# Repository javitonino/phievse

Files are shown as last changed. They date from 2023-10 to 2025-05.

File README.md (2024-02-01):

# ϕ-EVSE

An electric vehicle "charger" (EVSE) that can automatically switch between 1 and 3 phase charging.

**This is a personal learning project and it's not production ready. Use it at your own risk.** That said, this might be interesting to learn how this devices work.
Since I was learning myself when I designed this, it should be relatively easy to understand.

## Features

The main differentiator (and motivation for the project) is the ability to switch between 1-phase and 3-phase charging, thus supporting the full range of charging powers.
In the case of 230V AC, this means from 1.4kW (1 phase, 6A) to 22kW (3 phase, 32A).

Charging power can be controlled via web interface or MQTT (integrated with HomeAssistant).

## Anti-features (you really shouldn't connect your car to this)

Although there are safety checks in place (pilot and relay checks), I haven't been able to test them outside of lab conditions. As such, this should not be considered a safe product to use,
which is not ideal (to say the least) for something called Electric Vehicle Safety Equipment.

In general, I lost interest in the project once it behaved well enough to fulfill my needs, so things are not as stable as they should. 

Finally, there are some decisions (documented in the READMEs for [hardware](hardware/README.md) and [firmware](firmware/README.md)) that are not really good ideas and were done in an effort to understand why nobody
else was doing it that way.

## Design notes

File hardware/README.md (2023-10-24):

# ϕ-EVSE hardware

These are the schematics for the ϕ-EVSE project. See also the [project README](../README.md).

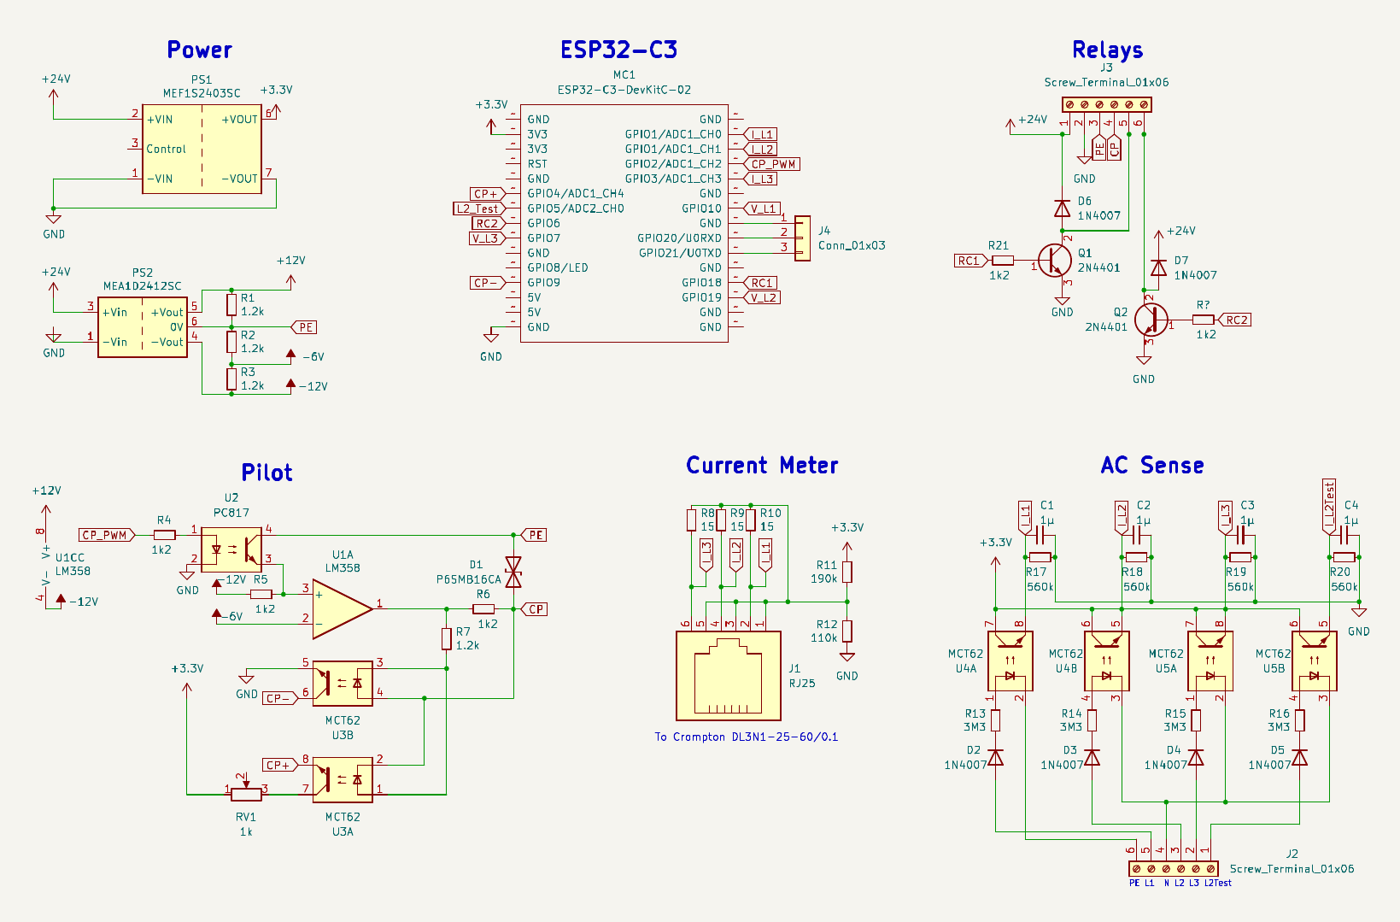
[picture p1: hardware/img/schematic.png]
Schematics


## Design notes

- The device is controlled by an ESP32-C3 microcontroller. In this case, it's using a devkit mounted into a prototype board.
- The power system generates 24V (for the relays), ±12V (for the control pilot) and 3.3V (for the electronics).
- The control pilot circuitry is optically isolated from the car. This difers from the standard control circuit and adding optocouples caused issues with switching speed and accurately setting the duty cycle.
- There is a current meter using a current transformer and shunt resistor connected to an ADC pin for each phase.
- There are four AC sensors (optocouplers with a capacitor for smoothing the signal). Three of them check the output of the relay (to check for stuck relays) and the forth one is used to check if 3-phase power is available at the input.

## Mounting

Everything is mounted on a DIN rail inside a CamdemBoss CHDX6-230 enclosure:
- 24V power supply, no special requirements.
- Enclosure for the electronic (CamdemBoss CNMB/2/KIT)
- Main power contactor: 4-pole contactor. Using Finder 22.74.0.024.1310 for the small size while supporting 32A.
- 1-3 phase contactor: 2-pole contactor. Using Finder 22.72.0.024.1310 for the small size while supporting 32A.

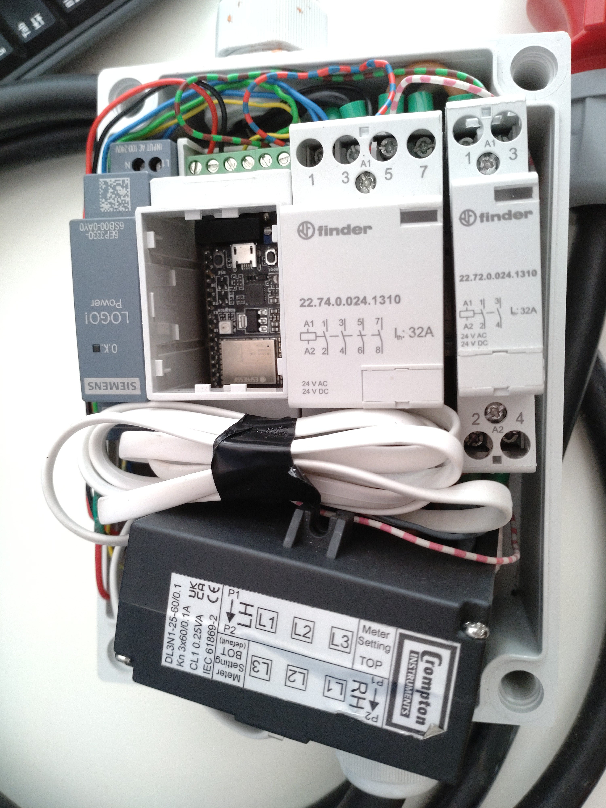
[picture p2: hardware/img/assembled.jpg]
Assembled EVSE


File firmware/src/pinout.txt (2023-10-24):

+24V    0V     PE     Pilot      R(18)     R(6)

RJ25   PE  Lpe(10)  N  Ln(19)  Ln(7)  Ln(5)

GPIO
====

In (analog)
-----------
Current Meter: 0, 1, 3
Pilot+: 4

In (digital)
------------
Voltage Meter (PE): 10
Voltage Meter (N): 19, 7, 5
Pilot-: 9

Out
---
LED: 8
Relays: 18, 6
PWM Pilot: 2

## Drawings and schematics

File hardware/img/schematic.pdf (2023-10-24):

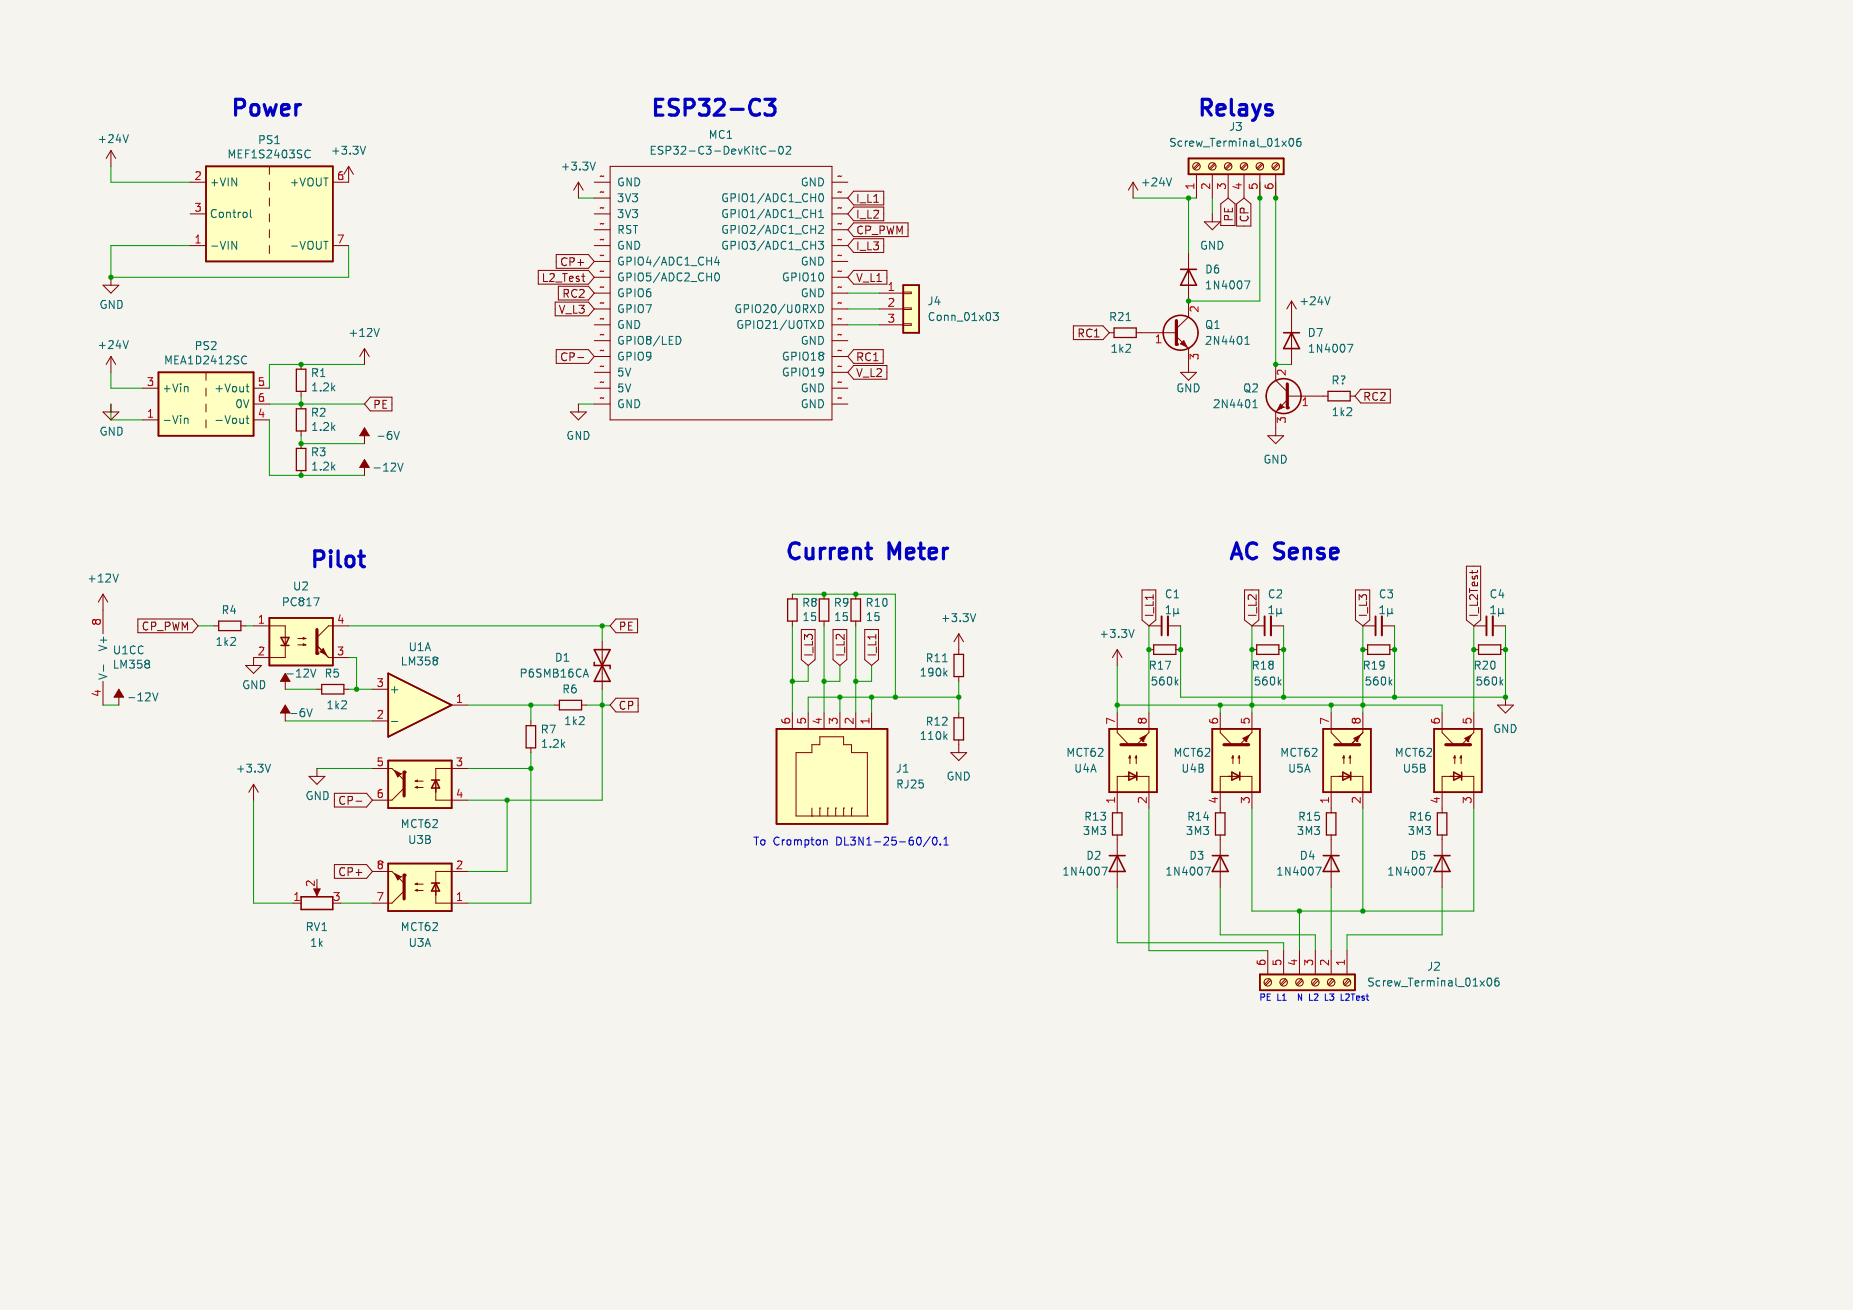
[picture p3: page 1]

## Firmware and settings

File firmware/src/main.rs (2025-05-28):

#![allow(unexpected_cfgs)]

use embedded_svc::ipv4::Configuration;
use embedded_svc::wifi::AccessPointConfiguration;
use esp_idf_hal::gpio::{PinDriver, Pull};
use esp_idf_hal::ledc::config::TimerConfig;
use esp_idf_hal::ledc::{LedcDriver, LedcTimerDriver, Resolution};
use esp_idf_hal::prelude::*;
use esp_idf_svc::eventloop::EspSystemEventLoop;
use esp_idf_svc::netif::{EspNetif, NetifConfiguration};
use esp_idf_svc::sntp::EspSntp;
use esp_idf_svc::wifi::WifiDriver;
use esp_idf_sys::*;
use phievse::driver::gpio::InterruptPin;
use phievse::gpio::RelayPin;
use phievse::*;
use std::error::Error;

// Using as library
use phievse::driver::{adc::*, watchdog::*};
use phievse::logger::RingBufferLogger;

// Using directly
mod config;
mod httpd;
mod mqtt;

use embedded_svc::{ipv4::DHCPClientSettings, wifi::ClientConfiguration};
use esp_idf_svc::{netif::NetifStack, wifi::EspWifi};

use crate::config::*;

esp_idf_sys::esp_app_desc! {}

fn main() -> Result<(), Box<dyn Error>> {
    // Disables USB JTAG on GPIO 18/19. Allows to disable pullups in those pins.
    unsafe {
        let usb_jtag_reg: *mut u32 = 1610887192 as *mut u32;
        let mask_bit_9 = u32::MAX - (1 << 9);
        *usb_jtag_reg &= mask_bit_9;
    }

    esp_idf_svc::sys::link_patches();

    // Set maximum priority after timers and driver code
    // Other spawned threads (e.g: LEDController) default to 5 unless changed
    unsafe { vTaskPrioritySet(std::ptr::null_mut(), 19) };

    // Initialize esp-idf-svc logger
    // EspLogger::initialize_default();

    // Initialize our in-memory logger
    let ring_logger: Box<RingBufferLogger> = Default::default();
    let ring_buffer = ring_logger.buffer.clone();
    log::set_boxed_logger(ring_logger)?;
    log::set_max_level(log::LevelFilter::Info);
    println!("Started logger");

    unsafe {
        let cfg = esp_pthread_cfg_t {
            stack_size: 4096,
            prio: 5,
            inherit_cfg: false,
            thread_name: std::ptr::null(),
            pin_to_core: 0,
        };
        esp_pthread_set_cfg(&cfg);
    }

    // Initialize all peripherals and the controller
    let peripherals = esp_idf_hal::peripherals::Peripherals::take().unwrap();
    let pins = peripherals.pins;

    let timer = LedcTimerDriver::new(
        peripherals.ledc.timer0,
        &TimerConfig::default()
            .frequency(1.kHz().into())
            .resolution(Resolution::Bits14),
    )?;

    let mut g10 = PinDriver::input(pins.gpio10)?;
    g10.set_pull(Pull::Floating)?;
    let mut g19 = PinDriver::input(pins.gpio19)?;
    g19.set_pull(Pull::Floating)?;
    let mut g7 = PinDriver::input(pins.gpio7)?;
    g7.set_pull(Pull::Floating)?;
    let mut g5 = PinDriver::input(pins.gpio5)?;
    g5.set_pull(Pull::Floating)?;
    let mut g9 = PinDriver::input(pins.gpio9)?;
    g9.set_pull(Pull::Up)?;

    let relay_main = RelayPin::new(LedcDriver::new(
        peripherals.ledc.channel1,
        &timer,
        pins.gpio6,
    )?);
    let relay_3_phase = RelayPin::new(LedcDriver::new(
        peripherals.ledc.channel2,
        &timer,
        pins.gpio18,
    )?);
    let analog = AdcDmaDriver::new(
        peripherals.adc1,
        pins.gpio3,
        pins.gpio1,
        pins.gpio0,
        pins.gpio4,
    )?;

    let control_pilot = LedcDriver::new(peripherals.ledc.channel0, &timer, pins.gpio2)?;
    let pilot_negative = InterruptPin::new(g9);
    let controller = Box::new(PhiEvseController::new(PhiEvsePeripherals {
        relay_main,
        relay_3_phase,
        v_sense: (g10, g19, g7),
        v_sense_3_phase: g5,
        analog,
        control_pilot,
        pilot_negative,
        watchdog: EspWatchdog,
    }));

    // Load configuration from NVS
    let config = PhiEvseConfig::load()?;
    println!("{config:#?}");

    // Build Wifi configurations
    let mut ap_config = AccessPointConfiguration {
        ssid: config.ap.ssid.as_str().try_into().unwrap(),
        ..Default::default()
    };
    if let Some(password) = config.ap.psk {
        ap_config.auth_method = embedded_svc::wifi::AuthMethod::WPA2Personal;
        ap_config.password = password.as_str().try_into().unwrap();
    }

    let mut needs_connect = false;
    let wifi_config = if let Some(sta) = config.sta {
        let mut sta_config = ClientConfiguration {
            ssid: sta.ssid.as_str().try_into().unwrap(),
            ..Default::default()
        };
        needs_connect = true;
        if let Some(password) = sta.psk {
            sta_config.auth_method = embedded_svc::wifi::AuthMethod::WPA2Personal;
            sta_config.password = password.as_str().try_into().unwrap();
        }

        embedded_svc::wifi::Configuration::Mixed(sta_config, ap_config)
    } else {
        embedded_svc::wifi::Configuration::AccessPoint(ap_config)
    };

    // Initialize Wifi
    let mut wifi_client_conf = NetifConfiguration::wifi_default_client();
    wifi_client_conf.ip_configuration = Some(Configuration::Client(
        embedded_svc::ipv4::ClientConfiguration::DHCP(DHCPClientSettings {
            hostname: Some(config.hostname.as_str().try_into().unwrap()),
        }),
    ));
    let wifi = Box::new(EspWifi::wrap_all(
        WifiDriver::new(peripherals.modem, EspSystemEventLoop::take()?, None)?,
        EspNetif::new_with_conf(&wifi_client_conf)?,
        EspNetif::new(NetifStack::Ap)?,
    )?);
    let wifi = Box::leak(wifi);
    wifi.set_configuration(&wifi_config)?;
    wifi.start()?;
    if needs_connect {
        wifi.connect()?;
    }

    // NTP
    let _ntp = EspSntp::new_default();

    // Initialize HTTP server
    println!("Starting HTTPd");
    let _h = httpd::start(
        ring_buffer,
        controller.status(),
        controller.control_channel(),
    )?;
    println!("HTTP running");

    if let Some(uri) = config.mqtt_uri {
        mqtt::start(&uri, controller.status(), controller.control_channel())?;
    }

    // Run
    Box::leak(controller).run();

    #[allow(unreachable_code)]
    Ok(())
}

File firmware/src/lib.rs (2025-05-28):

use adc::{AdcChannel, AdcSubscriber};
use control_pilot::{ControlPilotMode, ControlPilotReader, ControlPilotSignal, set_control_pilot};
use current_meter::CurrentMeter;
use embedded_hal::{PwmPin, digital::v2::InputPin};
use serde::Serialize;
use std::{
    cmp::min,
    fmt::Display,
    sync::{
        Arc, Mutex,
        atomic::{AtomicU32, Ordering},
        mpsc,
    },
    thread::sleep,
    time::Duration,
};

use gpio::{AlarmInput, AlarmReceiver, RelayPin};
use watchdog::Watchdog;

pub mod adc;
mod control_pilot;
mod current_meter;
pub mod gpio;
pub mod led;
pub mod logger;
pub mod watchdog;

#[cfg(target_arch = "riscv32")]
pub mod driver;

pub enum ControlMessage {
    SetMaxPower(u32),
    Shutdown,
}

pub struct PhiEvsePeripherals<A, CP, CPN, R1, R2, L1, L2, L3, L3S, W>
where
    A: AdcSubscriber,
    CP: PwmPin,
    CPN: AlarmInput,
    R1: PwmPin<Duty = u32> + Send,
    R2: PwmPin<Duty = u32> + Send,
    L1: InputPin,
    L2: InputPin,
    L3: InputPin,
    L3S: InputPin,
    W: Watchdog,
{
    // /// Main contactor
    pub relay_main: RelayPin<R1>,
    // /// Relay that switches phases 2 and 3 (to switch between 1 and 3 phase mode)
    pub relay_3_phase: RelayPin<R2>,
    /// Current meters for each phase + Control Pilor voltage
    pub analog: A,
    // pilot_positive: xxx
    // /// Control pilot -12v meter (diode check)
    pub pilot_negative: CPN,
    // /// Control pilot PWM pin
    pub control_pilot: CP,
    // /// Voltage sense for each phase
    pub v_sense: (L1, L2, L3),
    // /// 3-phase voltage sense
    pub v_sense_3_phase: L3S,

    pub watchdog: W,
}

#[derive(PartialEq, Debug, Copy, Clone, Default, Serialize)]
pub enum PhiEvseState {
    #[default]
    NotConnected,
    Connected,
    Ready,
    Charging,
    Error,
    Stopping,
    ShuttingDown,
    Shutdown,
}

impl Display for PhiEvseState {
    fn fmt(&self, f: &mut std::fmt::Formatter<'_>) -> std::fmt::Result {
        f.write_fmt(format_args!("{self:?}"))
    }
}

#[derive(Clone, Default, Serialize)]
pub struct PhiEvseStatus {
    pub power: u32,
    pub state: PhiEvseState,
    pub max_power: u32,
}

pub struct PhiEvseController<A, CP, CPN, R1, R2, L1, L2, L3, L3S, W>
where
    A: AdcSubscriber,
    CP: PwmPin,
    CPN: AlarmInput,
    R1: PwmPin<Duty = u32> + Send,
    R2: PwmPin<Duty = u32> + Send,
    L1: InputPin,
    L2: InputPin,
    L3: InputPin,
    L3S: InputPin,
    W: Watchdog,
{
    peripherals: PhiEvsePeripherals<A, CP, CPN, R1, R2, L1, L2, L3, L3S, W>,

    current: [AtomicU32; 3],
    control_pilot: ControlPilotReader,
    state: PhiEvseState,
    max_power: u32,
    max_current: u32,
    three_phase: bool,
    current_adjustment: i32,

    status: Arc<Mutex<PhiEvseStatus>>,

    control_tx: mpsc::Sender<ControlMessage>,
    control_rx: mpsc::Receiver<ControlMessage>,
}

impl<A, CP, CPN, R1, R2, L1, L2, L3, L3S, W>
    PhiEvseController<A, CP, CPN, R1, R2, L1, L2, L3, L3S, W>
where
    A: AdcSubscriber,
    CP: PwmPin<Duty = u32>,
    CPN: AlarmInput,
    R1: PwmPin<Duty = u32> + Send,
    R2: PwmPin<Duty = u32> + Send,
    L1: InputPin,
    L2: InputPin,
    L3: InputPin,
    L3S: InputPin,
    W: Watchdog,
{
    pub fn new(peripherals: PhiEvsePeripherals<A, CP, CPN, R1, R2, L1, L2, L3, L3S, W>) -> Self {
        let (tx, rx) = mpsc::channel();

        Self {
            current: Default::default(),
            peripherals,
            control_pilot: Default::default(),
            state: PhiEvseState::NotConnected,
            max_power: 0,
            max_current: 0,
            three_phase: false,
            status: Default::default(),
            current_adjustment: 0,
            control_tx: tx,
            control_rx: rx,
        }
    }

    pub fn status(&self) -> Arc<Mutex<PhiEvseStatus>> {
        self.status.clone()
    }

    pub fn control_channel(&self) -> mpsc::Sender<ControlMessage> {
        self.control_tx.clone()
    }

    pub fn run(&'static mut self) -> ! {
        let mut set_control_pilot =
            |signal| set_control_pilot(&mut self.peripherals.control_pilot, signal);

        // Initialize current meters / ADC
        let mut current_meters = [
            CurrentMeter::new(&self.current[0], 0.8),
            CurrentMeter::new(&self.current[1], 1.4),
            CurrentMeter::new(&self.current[2], 1.6),
        ];
        let cp = &self.control_pilot;
        self.peripherals.analog.subscribe(move |c, d| match c {
            AdcChannel::CurrentL1 => current_meters[0].receive(d),
            AdcChannel::CurrentL2 => current_meters[1].receive(d),
            AdcChannel::CurrentL3 => current_meters[2].receive(d),
            AdcChannel::ControlPilot => cp.receive(d),
        });

        // Initialize CP negative alarm
        let cp_negative = &self.control_pilot.negative;
        self.peripherals
            .pilot_negative
            .subscribe(AlarmReceiver(Box::new(|| {
                cp_negative.store(true, std::sync::atomic::Ordering::Relaxed)
            })));

        set_control_pilot(ControlPilotSignal::Standby);

        // TODO: Safety checks

        // Wait for everything to settle before reading CP and enabling watchdogs/alarms
        sleep(Duration::from_millis(500));
        self.peripherals.pilot_negative.arm();
        self.peripherals.watchdog.init(Duration::from_secs(2));

        // State machine
        let mut i = 0;
        let mut changing_power = false;
        let mut next_current_adjustment = 0;
        let mut prev_state = PhiEvseState::NotConnected;
        let mut stop_timeout = 0;
        loop {
            i = (i + 1) % 50;
            self.peripherals.watchdog.reset();

            let total_mamps: u32 = self.current.iter().map(|c| c.load(Ordering::Relaxed)).sum();
            self.status.lock().unwrap().power = total_mamps * 230 / 1000;
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

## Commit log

2023-10-24 Cleanup for initial release
    [partitions.csv, phievse.kicad_sch]
2025-05-25 Update to esp 5.2
    Squashed commit of the following:
    commit 51543f7b1fb642920f00ebc8697fedf20c46cdba
    Author: Javier Torres <javier@javiertorres.eu>
    Date: Sun May 25 23:30:16 2025 +0200
    Finishing touches
    commit 3a5ffac33efaa951cfd5eac8d85c4b52d4096f24
    Author: Javier Torres <javier@javiertorres.eu>
    Date: Tue May 20 18:13:07 2025 +0200
    Fix MQTT, it compiles
    commit 3c191eef316fcbca9c237924864c05dda1c8428b
    Author: Javier Torres <javier@javiertorres.eu>
    Date: Tue May 20 18:08:13 2025 +0200
    Update http
    commit 8b2ebf4f6820e874280786cbaf39954062c201d0
    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
    [partitions.csv]
2025-05-28 Simpler CurrentMeter to use less CPU
2025-05-28 Avoid getting stuck in ready state
    [lib.rs]
